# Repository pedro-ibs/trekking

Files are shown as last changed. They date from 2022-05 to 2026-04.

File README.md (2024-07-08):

# Trekking project
Desenvolvimento de um robô rádio-controlado/autônomo da moralidade “trekking”

Nos arquivos [anteriores-descontinuados](./anteriores-descontinuados/) e nos demais arquivos deste repositório podem conter os termos `rv1` e `rv2` eles estão referindo a versões anteriores do robô sendo `Robô versão 1` `Robô versão 2`.

<br>

Apresentações anteriores relaionadas:
 * [**#CPBR16** - Trabalhando com Unidades de medidas Inerciais (IMU) ](https://garoa.net.br/wiki/Dumont_Hackerspace_na_Campus_Party_2024)
 * [ **#CPBR15** - Construindo um Robô Trekking - versão 2.0](https://www.youtube.com/watch?v=lGhopql1V54)
 * [ **#CPBR14** - Construção de um robo rádio controlado](https://www.youtube.com/watch?v=8P9nPsCdVAc)

<br> <br> <br>

### **Robô versão 3**:
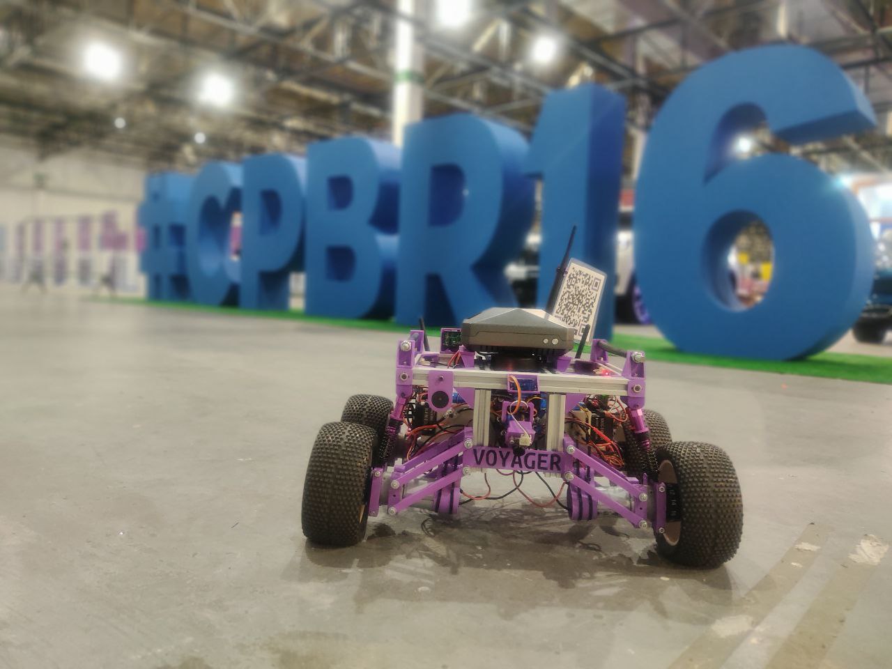
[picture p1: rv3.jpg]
Robô versão 2


<br>

### **Robô versão 2**: 

Robô versão 2

<br>

### **Robô versão 1**: 

Robô versão 1

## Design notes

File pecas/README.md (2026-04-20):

# Peças
Todas as peças do projeto foram desenvolvidas utilizado o software [FreeCad](https://www.freecadweb.org/).

 * *[Medidas](./medidas)*
 * *[Peças 3D](./stl)*
 * Cor da montagem HEX: ```#380054``` 

### *Peças externas*

Algumas peças já existentes utilizadas no projeto

  * [Porca para perfil V-slot 20x20](https://www.thingiverse.com/thing:3050607)
  * [Star Trek Pin](https://www.thingiverse.com/thing:2798431)

<hr><br><br>

# Fabricação

Todas as peças foram fabricadas utilizando uma prototipadora Creality Ender-3, e fatiados pelo programa Ultimaker Cura.

#### Especificações *gerais* de impressão:

<br>

Parâmetro               | Valor
:---------------------- | :-------------------------------------
Adesão                  | Ativado
Nozzle                  | 0.4 mm
Densidade               | 30 %
Resolução               | 0.2

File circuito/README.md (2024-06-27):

# **ESQUEMA GERAL DA ALIMENTAÇÃO E CONEXÇÕES DO ROBÔ**

<br>

### **ALIMENTAÇÃO GERAL**
A chave `SELETOR` muda se a bateria passrá pelo voltimetro-amperimetro, ou se firará em paralelo com a carga, permitindo assim monitorar o carregamento da bateria. Também com as chaves `CIRCUITO COMUTADOR` e `CIRCUITO POTÊNCIA` permite ligar ou desligar um sistema independentemente do outro. Essas opções existem para facilitar o desenvolvimento e manutenção do robô

<br>

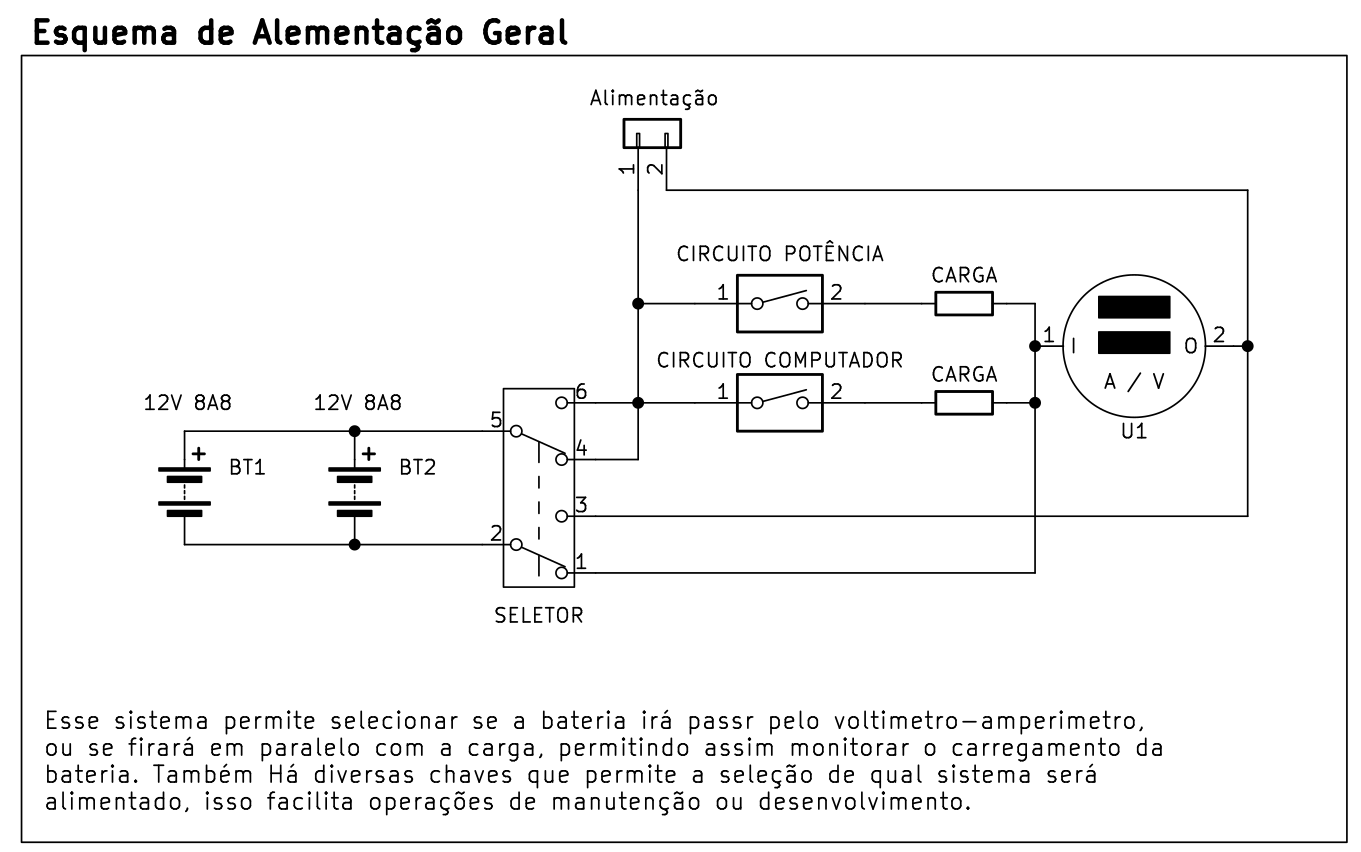
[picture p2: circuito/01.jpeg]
ALIMENTAÇÃO GERAL


<br> <br>

### **ALIMENTAÇÃO DOS SUBSISTEMAS**
Para o Robô a linha de `POTÊNCIA` é considerada a de 12V, que irá alimentar os motores e atuadores que demandam uma corrente elevada. Já a linha `COMPUTADOR` é responsável por alimentar o sistema de controle principal e alguns subsistemas.

<br>

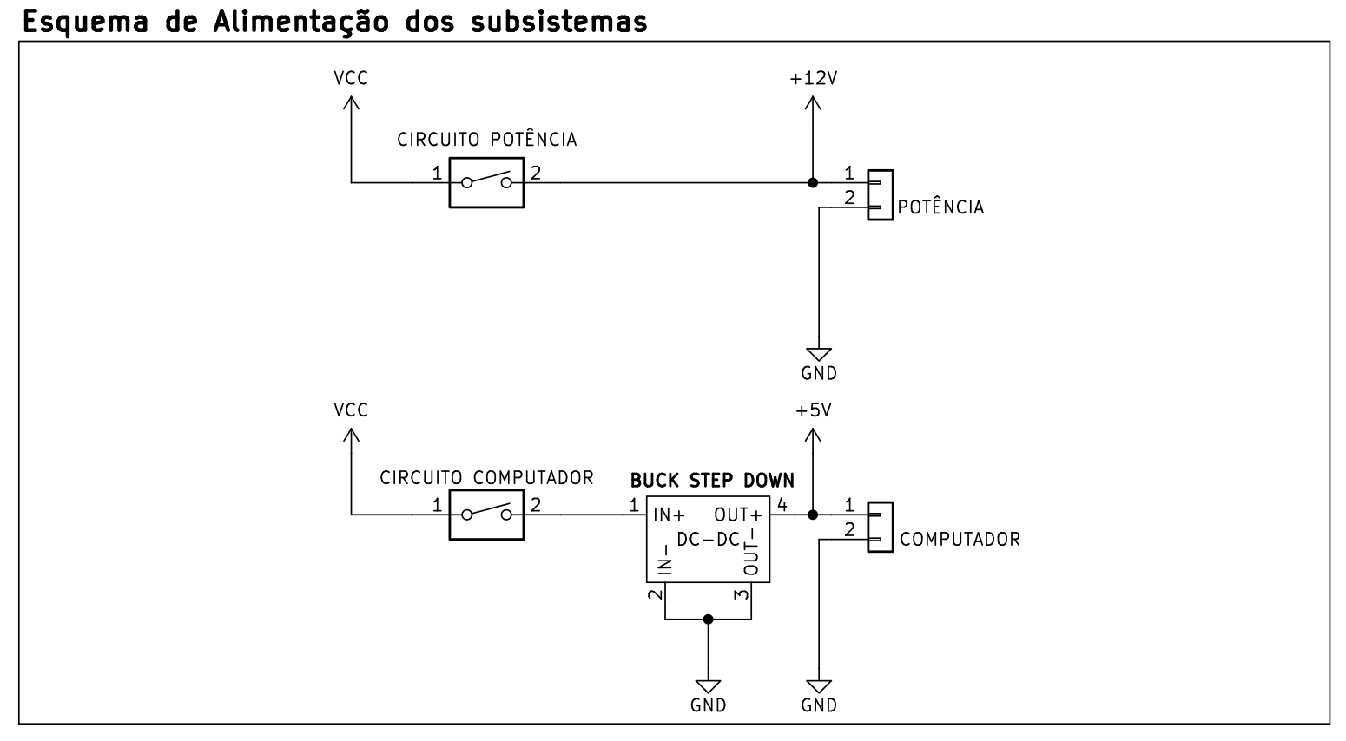
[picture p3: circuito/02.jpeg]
ALIMENTAÇÃO DOS SUBSISTEMAS


<br> <br>

### **ALIMENTAÇÃO DOS SUBSISTEMAS**
O robô contém alguns subsistemas, dois reservados para controlar os conjuntos de motores esquerdos e direitos, e um responsável pelo controle de ativação e controle ativo sensores e atuadores, também faz a aquisição de alguns sensores.

<br>

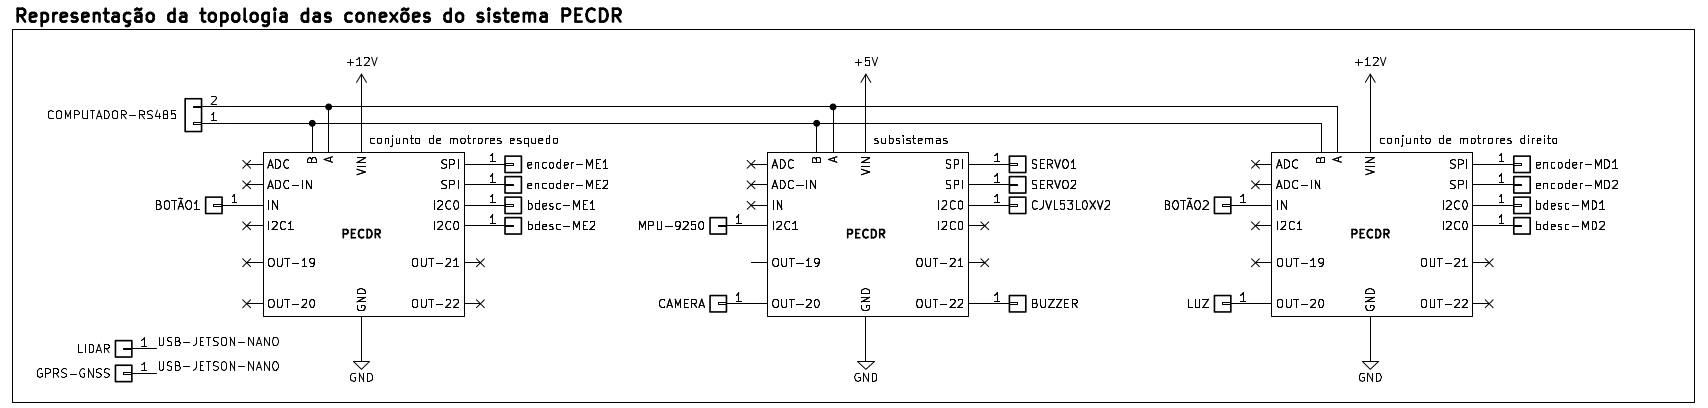
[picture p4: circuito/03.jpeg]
TOPOLOGIA E CONEXÕES DOS SUBSISTEMAS


<br>

### **Topologia das conexõesdo dos motores**

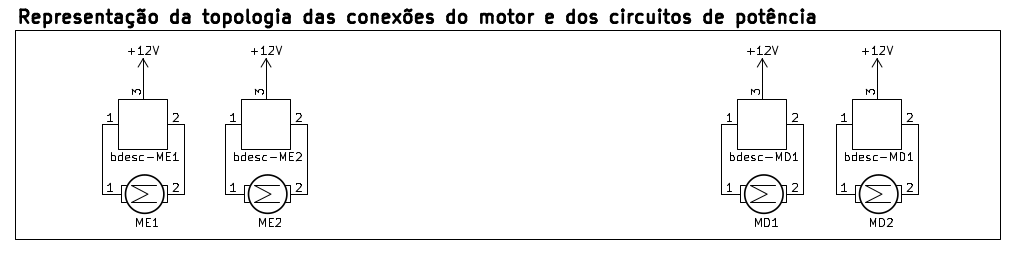
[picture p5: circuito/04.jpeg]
Topologia das conexõesdo dos motores


<br> <br>

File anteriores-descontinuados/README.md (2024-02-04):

# **Anteriores / Descontinuados**

Conforme as alterações e evolução do robô algumas ideias foram descontinuadas, então aqui contém alguns arquivos de versões passadas como circuitos, peças e configurações. Não há intenção de mexer ou documentar mais esses arquivos já que eles não fazem mais parte do robô.

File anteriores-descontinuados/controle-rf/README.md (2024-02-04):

# **controle-rf**

<br>

Testes de um controle RF construído para controlar o robô em longas distâncias. O controle utiliza o `Modulo Rf 433mhz Wireless Hc-12` e uma `microbit v1`.

<br>

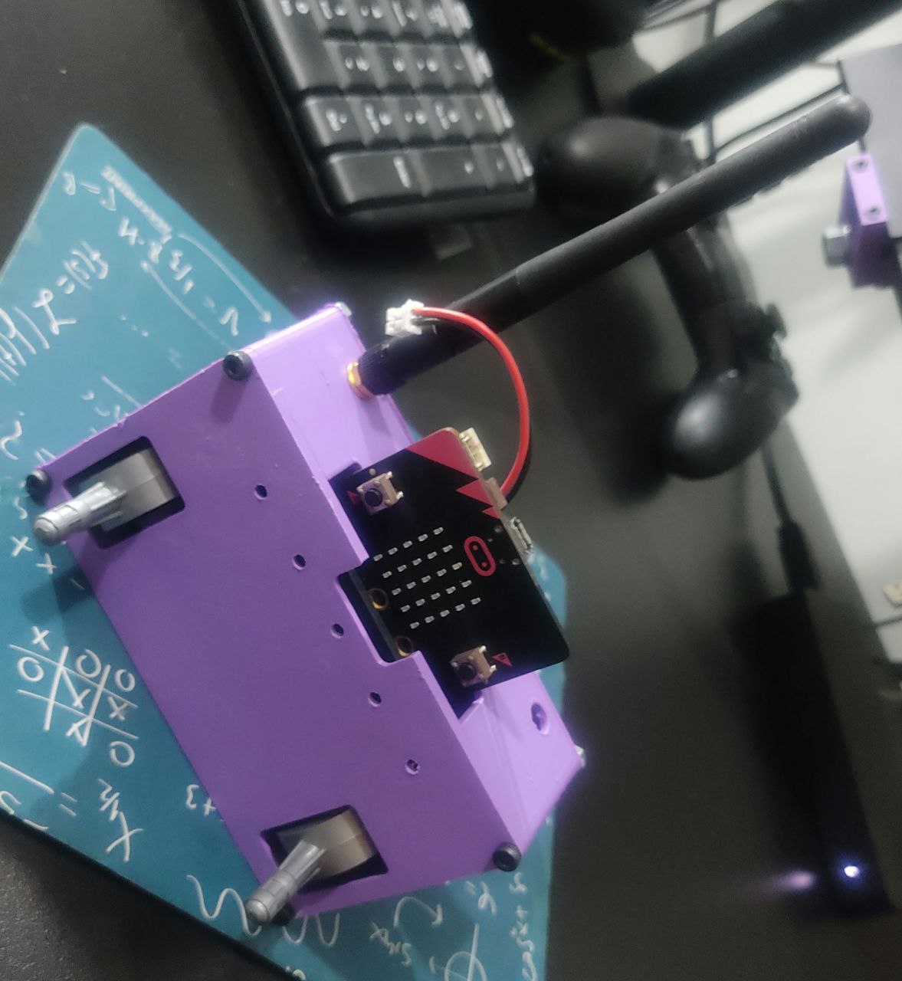
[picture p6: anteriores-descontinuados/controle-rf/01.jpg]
trekking vista da base e suporte da base


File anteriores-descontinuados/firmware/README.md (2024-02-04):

# **Firmware**

1. [**`NANO_BLE_33S`**](./NANO_BLE_33S): Auxiliar na aquisição de dados dos sensores.

2. [**`RPI_PICO_SDK`**](./RPI_PICO_SDK/): Controle dos motores e possível modulo de expansão. Tem acesso aos drivers dos motores portando responsável pelo controle dos mesmos.

## **Componentes**

O Trekking é composto por alguns dispositivo dentre sensores e computador e microcontroladores:

 * [Raspberry Pi 3 Model B](https://www.raspberrypi.com/products/raspberry-pi-3-model-b/)
 * [Raspberry Pi Pico](https://www.raspberrypi.com/products/raspberry-pi-pico/)
 * [Arduino Nano 33 BLE Sense](https://docs.arduino.cc/hardware/nano-33-ble-sense)
   * [IMU 9 Eixos LSM9DS1](https://content.arduino.cc/assets/Nano_BLE_Sense_lsm9ds1.pdf)
   * [Barometro LPS22HB](https://content.arduino.cc/assets/Nano_BLE_Sense_lps22hb.pdf)
   * [Sensor de Temperaura e Umidade HTS221](https://content.arduino.cc/assets/Nano_BLE_Sense_HTS221.pdf)
   * [Sensor de Gestos APDS-9960](https://content.arduino.cc/assets/Nano_BLE_Sense_av02-4191en_ds_apds-9960.pdf)
   * [Microfone MP34DT05](https://content.arduino.cc/assets/Nano_BLE_Sense_mp34dt05-a.pdf)
 * [GPRS GT-U7](https://manuals.plus/goouuu/goouuu-tech-gt-u7-gps-modules.pdf)
 * [Sensor de distância CJVL53L0XV2 / VL53L0X](https://www.st.com/resource/en/datasheet/vl53l0x.pdf)

 Esses dispositivo estão interconectados através das comunicações serias *usart*, *i2c* e *swd* como mostra o diagrama abaixo:

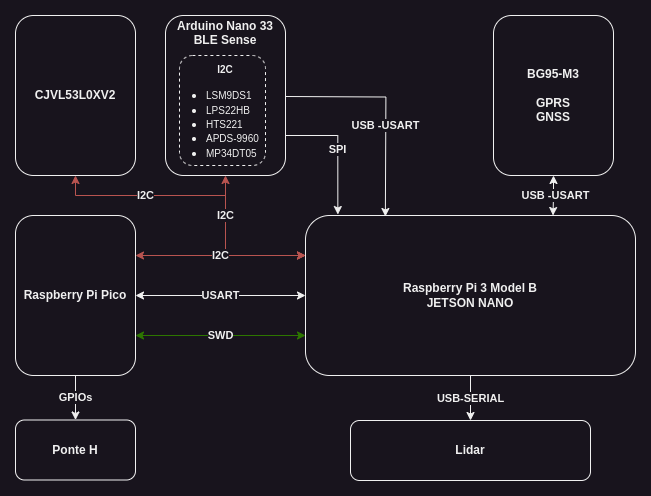
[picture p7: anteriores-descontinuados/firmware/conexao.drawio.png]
Rede de conexão entre os sensores e dispositivos do trekking


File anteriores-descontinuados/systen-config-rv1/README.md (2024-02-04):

# **NOTA:** 

<br>

Pode haver incoerências no processo e ou incompatibilidade nos funcionamentos pois esses arquivos retratam uma versão antiga e descontinuada do robô, eles estão aqui por uma questão de histórico.

<br><br><br>

# **systen-config-rv1**

<br>

1. Instale es dependências:

```
sudo apt update -y
sudo apt upgrade -y
sudo apt install python3-pip evdev -y

pip3 install evdev 
pip3 install pyserial 
```

2. copie o arquivo `gameped.py` para o diretório:

```
mkdir -p ~/trekking
cp gameped.py ~/trekking/gameped.py
```

3. Terne o arquivo executável:

```
sudo chmod +x ~/trekking/gameped.py
```

4. edite o arquivo `/etc/rc.local` antes da linha com o comando `exit` e insira o seguinte comando:
```
sudo python3  ~/trekking/gameped.py &
```

5. Reinicie a raspberry e logo após um tempo insira o adaptador do controle ela irá reconhecer automaticamente 

### **NOTA:**
Foi utilizado o controle `Ipega 9076` para esse programa.

6. Intale o node-red seguindo esses [paços](https://nodered.org/docs/getting-started/raspberrypi).

7. Importe o [flows-RASPBERRY_PI.json](./flows-RASPBERRY_PI.json) para o node-red.

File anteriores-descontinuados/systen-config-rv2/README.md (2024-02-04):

# **NOTA:** 

<br>

Pode haver incoerências no processo e ou incompatibilidade nos funcionamentos pois esses arquivos retratam uma versão antiga e descontinuada do robô, eles estão aqui por uma questão de histórico. 

<br><br><br>

# **systen-config-rv2**

<br>

1. Instale es dependências:

```
sudo apt update -y
sudo apt upgrade -y
sudo apt install python3-pip evdev -y

pip3 install evdev 
pip3 install pyserial 
```

2. Com o arquivo `gameped-rv2.py` e `gamepad-rv2-server.service` crie um no sistema por meio do systemctl.

3. Intale o node-red seguindo esses [paços](https://nodered.org/docs/getting-started/raspberrypi).

4. Importe o [flows-JETSON_NANO.json](./flows-JETSON_NANO.json) para o node-red.

### **NOTA:**
Foi utilizado o controle `Ipega 9076` para esse programa.

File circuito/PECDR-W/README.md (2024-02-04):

# **PECDR** - **P**lataforma **E**letrónica de **C**ontrole **D**istribuído em **R**ede 

A proposta deste circuito é distribuir o controle em subsistemas utilizando rede sem fio ou por meio da comunicação RS485. Conta com a `raspberry pi pico` modelo comum ou `W`. e diversos periféricos possibilitando atuar em trabalhos variados.

### **Elementos**:
 * O circuito embarca uma `raspberry pi pico` modelo comum ou `W`;
 * Uma fonte dc-dc buck step down 3V3 3A;
 * Driver de potência  L298N (com seleção de tensão de operação entre VCC e 3V3);
 * Interface de comunicação RS485;
 * Disponibiliza GPIOS para uso geral; 
 * Expansão para o MPU9250/6500;

<br>

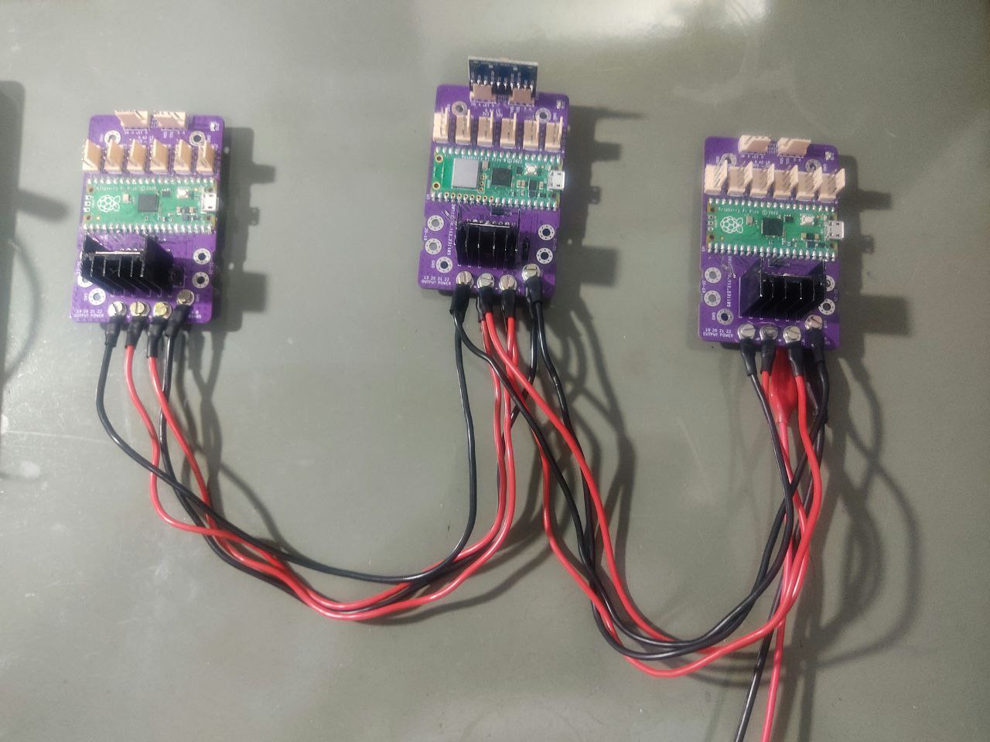
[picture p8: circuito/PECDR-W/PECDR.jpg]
imagem do circuito em rede RS485


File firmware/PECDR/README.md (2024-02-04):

# **PECDR** - **P**lataforma **E**letrónica de **C**ontrole **D**istribuído em **R**ede 

<br>

Veja a documentação do circuito [aqui](../../circuito/PECDR-W/README.md).

<br>

O robô está dividido em diversos subsistemas, como conjunto de motores esquerdo,  conjunto de motores direito e outros subsistemas. Onde o sistema de controle principal controla os subsistemas por meio de uma Rede em barramento com RS485.

<br> <br>

## **NOTA**:
Essas firmwares ainda estão em desenvolvimento e os arquivos aqui presente são para o início da organização deles.

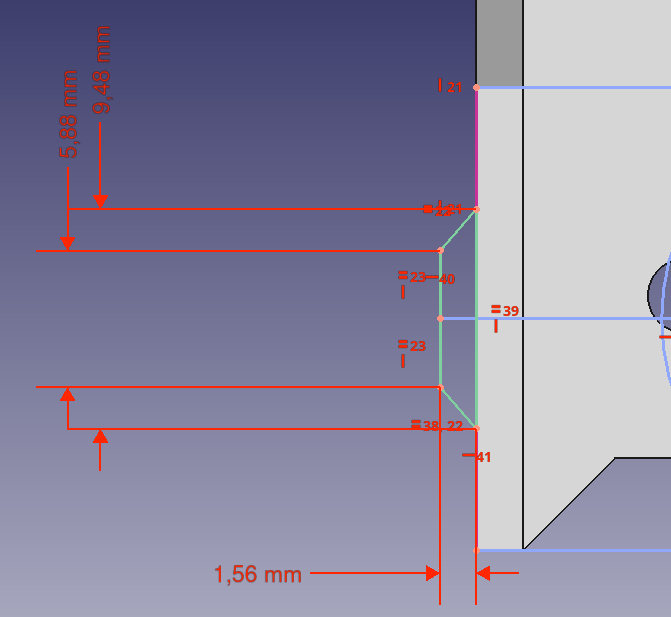
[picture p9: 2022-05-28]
pecas/medidas-trilho-rev2.png

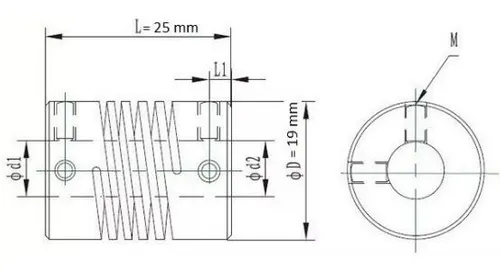
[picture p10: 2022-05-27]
anteriores-descontinuados/pecas/motor-rv1/medidas-acoplamento.webp

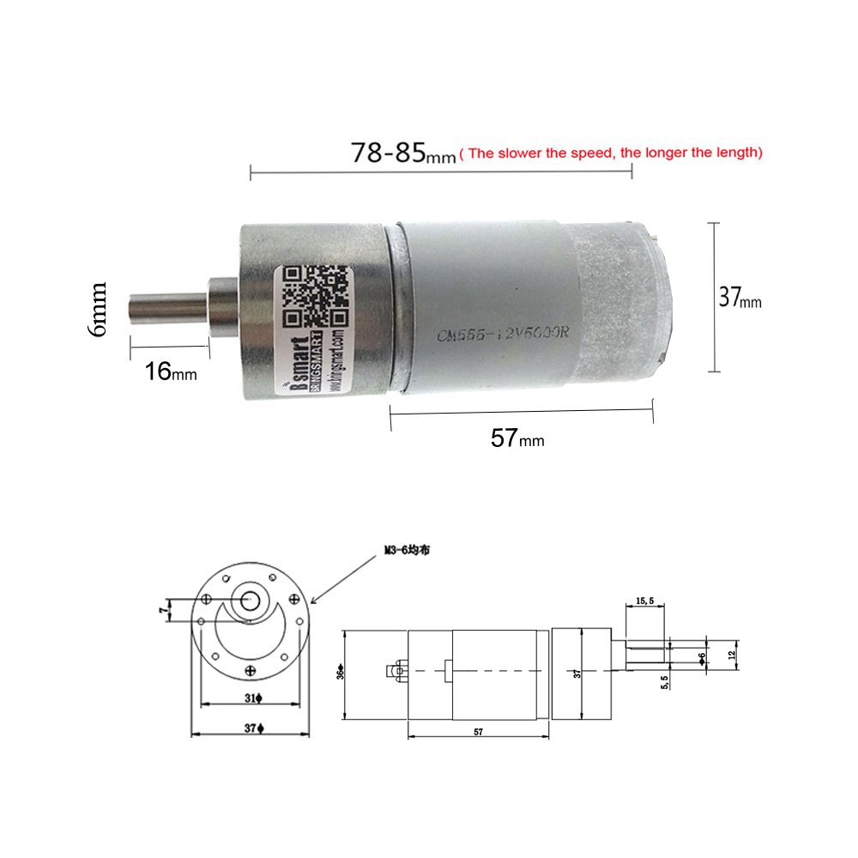
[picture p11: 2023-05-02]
anteriores-descontinuados/pecas/motor-rv2/motor2.jpg

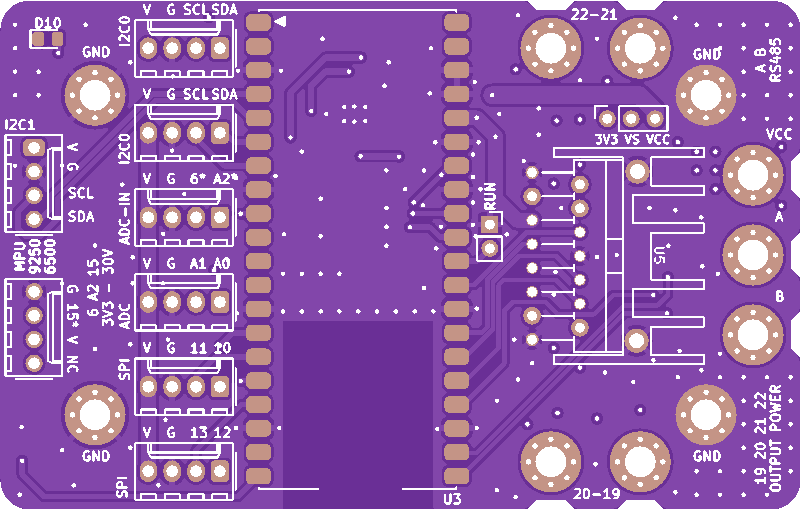
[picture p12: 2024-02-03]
circuito/PECDR-W/unnamed.png

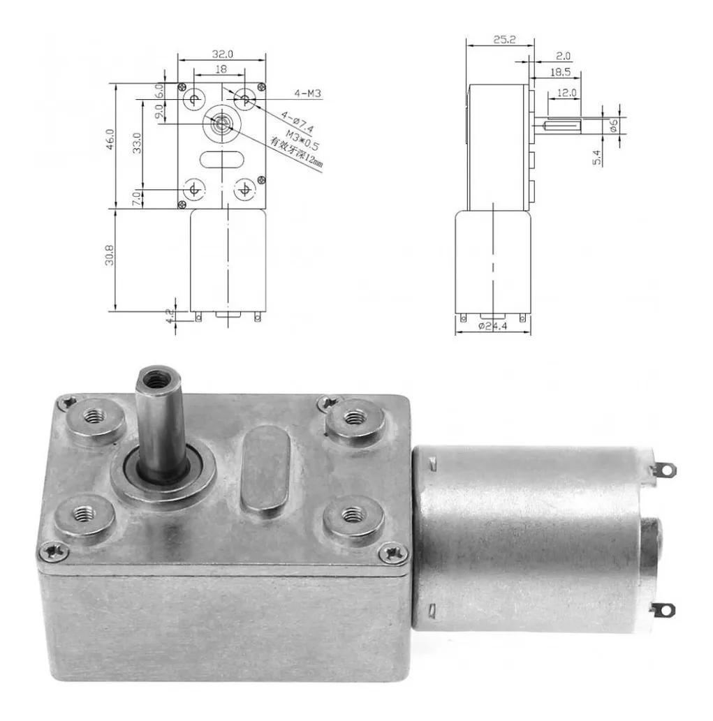
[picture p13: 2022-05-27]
anteriores-descontinuados/pecas/motor-rv1/madidas-motor.webp

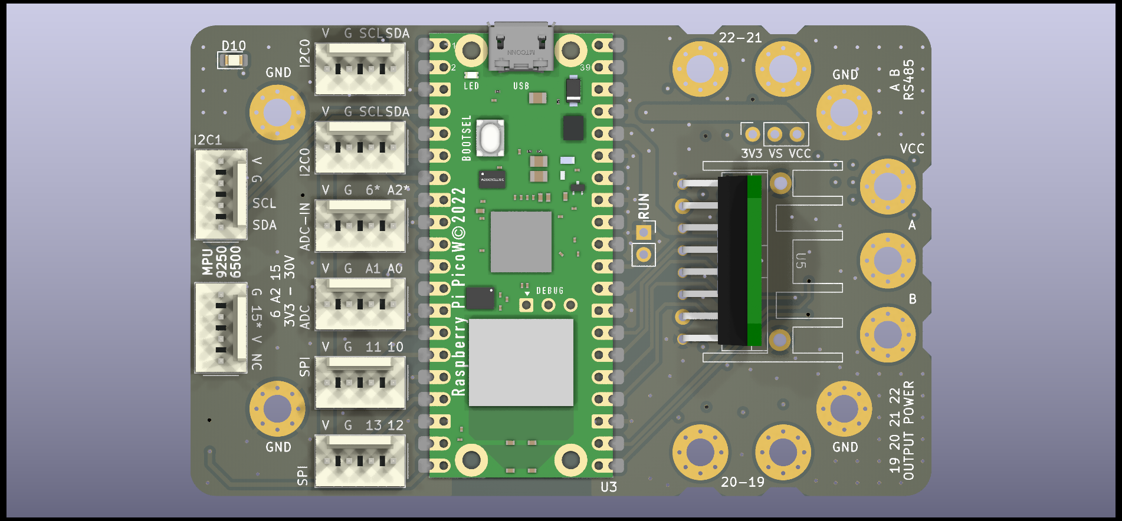
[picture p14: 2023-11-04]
circuito/PECDR-W/F-PECDR.png

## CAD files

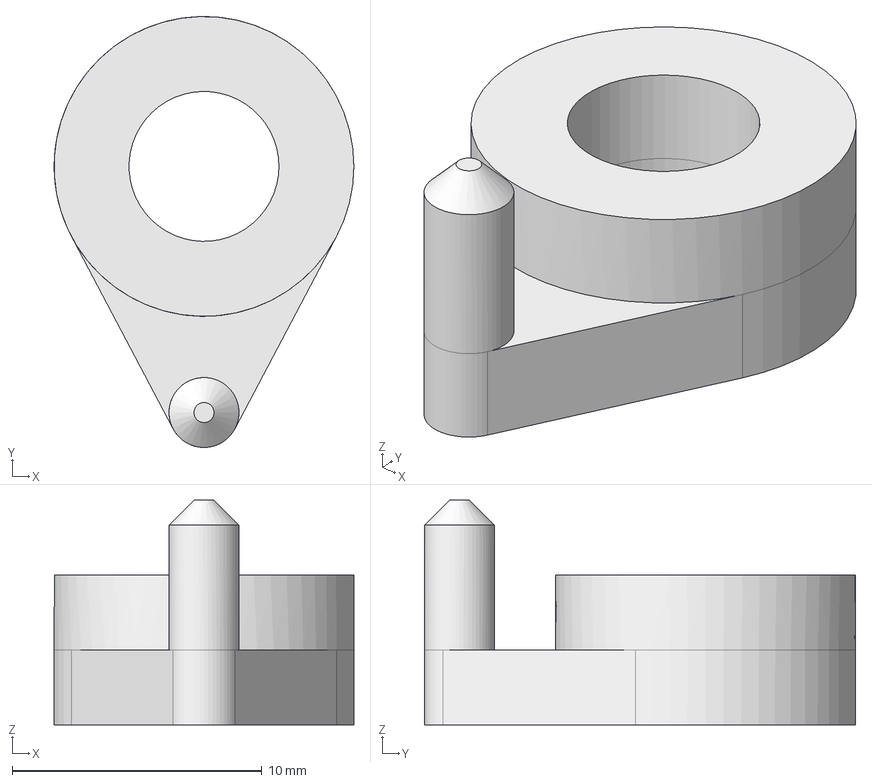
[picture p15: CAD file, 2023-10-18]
anteriores-descontinuados/controle-rf/peças/knob-pot.FCStd
12.0 x 17.2 x 9.00 mm

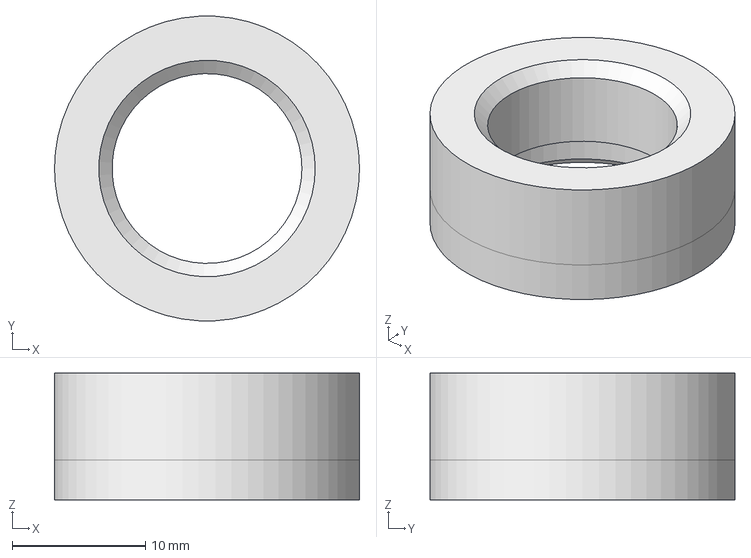
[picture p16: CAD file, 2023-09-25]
anteriores-descontinuados/pecas/camera-fpv-rv2/fisheye-coupling.FCStd
22.9 x 22.9 x 9.50 mm

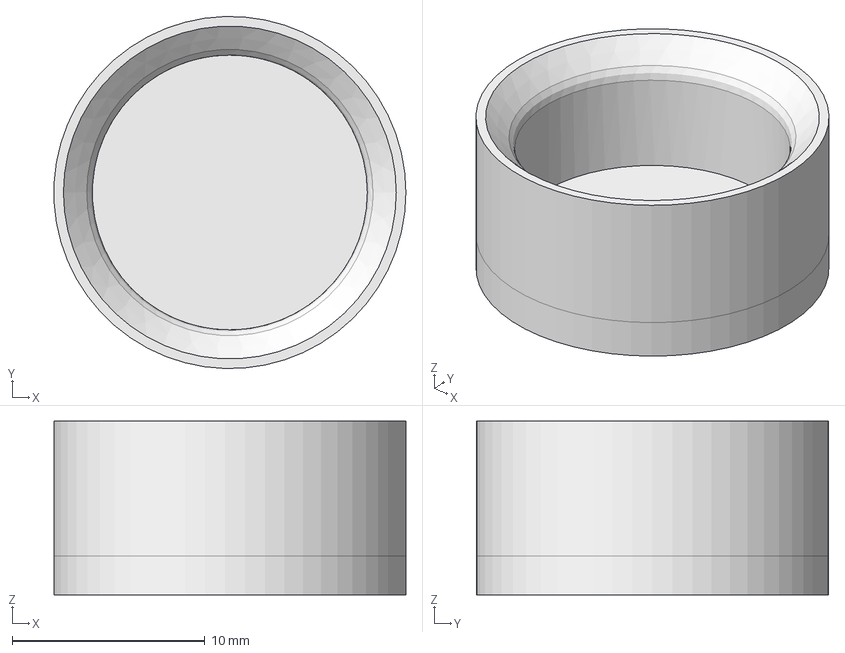
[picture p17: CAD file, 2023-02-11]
anteriores-descontinuados/pecas/camera-pi-infrared/fixed/cap.FCStd
18.2 x 18.2 x 9.00 mm

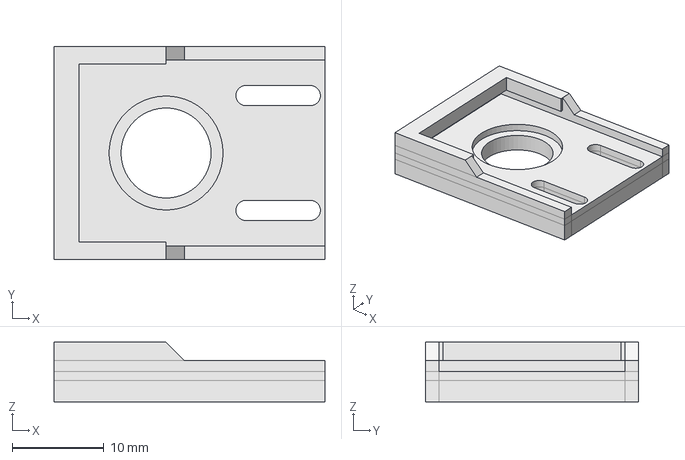
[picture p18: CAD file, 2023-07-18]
anteriores-descontinuados/pecas/camera-pi-infrared/magnetic-plug/case-lamp-base.FCStd
29.5 x 23.2 x 6.50 mm

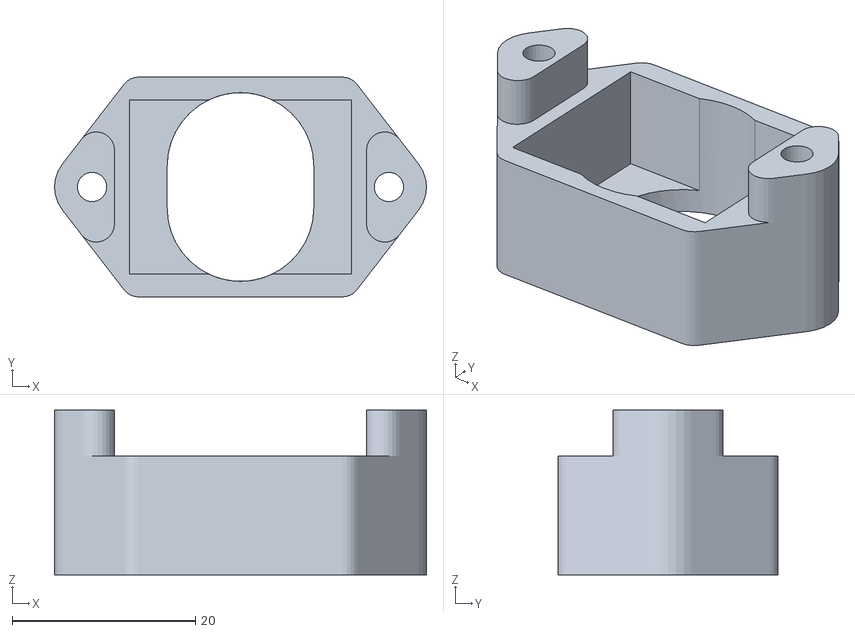
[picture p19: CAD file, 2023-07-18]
anteriores-descontinuados/pecas/camera-pi-infrared/stl/case-cam-shiled.stl
40.6 x 24.0 x 18.0

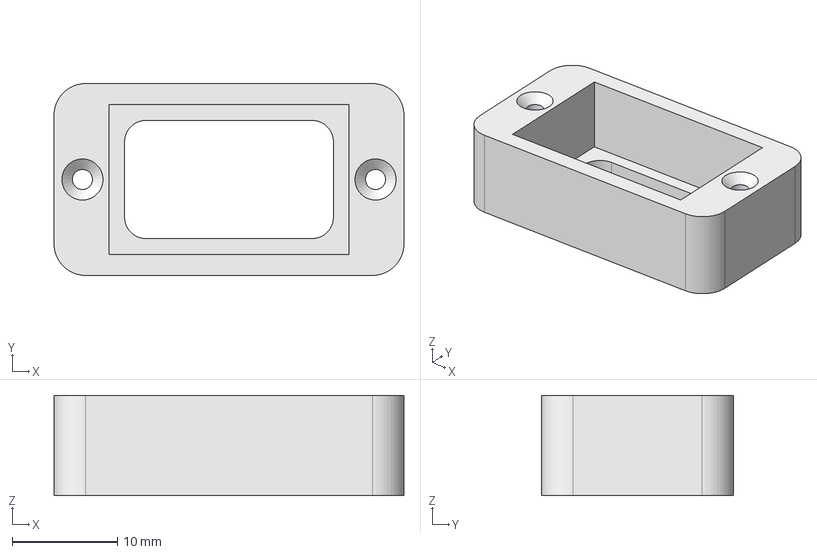
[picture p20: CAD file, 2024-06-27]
anteriores-descontinuados/pecas/case-multimetro-rv3/tampa.FCStd
33.2 x 18.2 x 9.50 mm

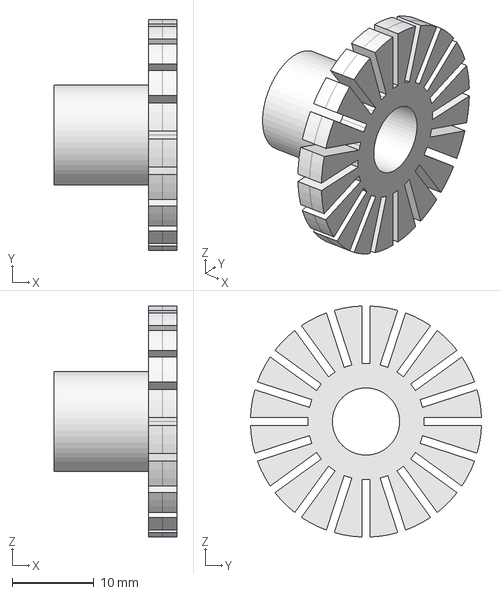
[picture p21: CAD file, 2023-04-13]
anteriores-descontinuados/pecas/encoder-rv1/disco-8d2-20P.FCStd
15.0 x 28.2 x 28.2 mm

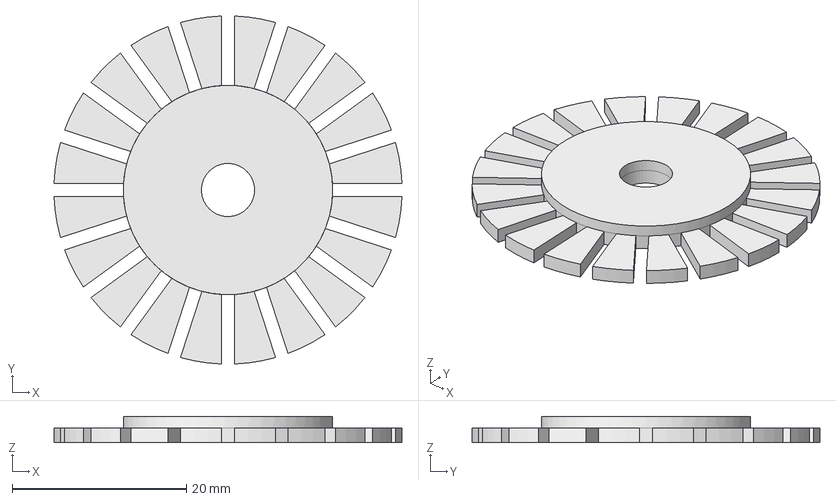
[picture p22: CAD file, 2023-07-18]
anteriores-descontinuados/pecas/encoder-vr2/disco-3d40-20P.FCStd
40.0 x 40.0 x 3.00 mm

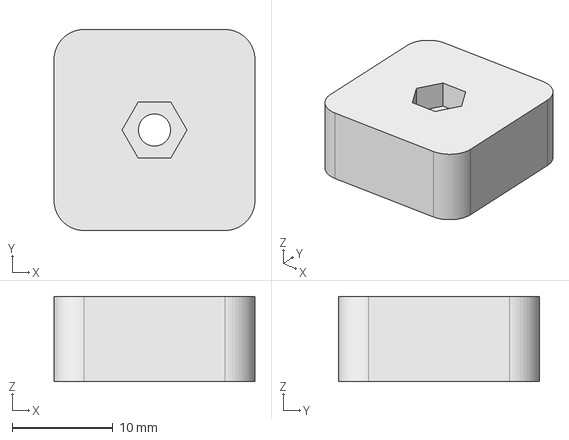
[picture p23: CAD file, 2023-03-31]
anteriores-descontinuados/pecas/lds-rv2/fixador.FCStd
20.0 x 20.0 x 8.50 mm

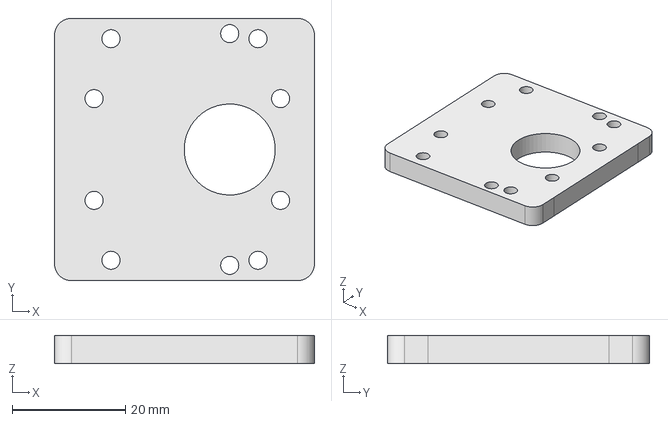
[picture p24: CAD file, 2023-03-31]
anteriores-descontinuados/pecas/motor-rv1/mancal-tras.FCStd
46.0 x 46.4 x 5.00 mm

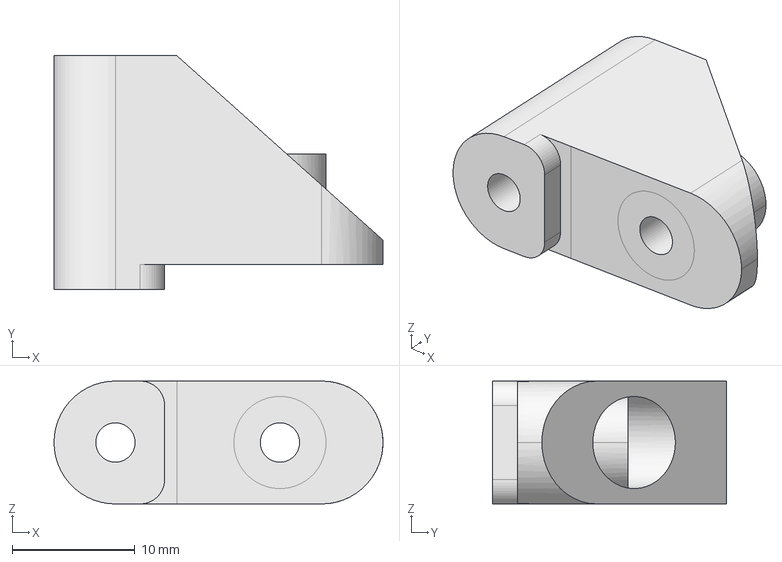
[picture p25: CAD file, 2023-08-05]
anteriores-descontinuados/pecas/motor-rv2/haste-articulada.FCStd
26.8 x 19.0 x 10.0 mm

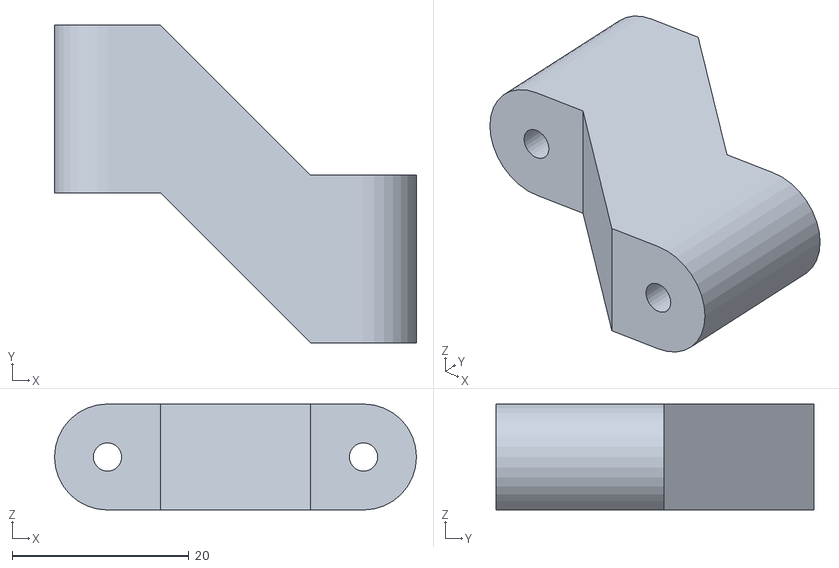
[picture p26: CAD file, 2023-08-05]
anteriores-descontinuados/pecas/motor-rv2/stl/haste.stl
41.0 x 36.0 x 12.0

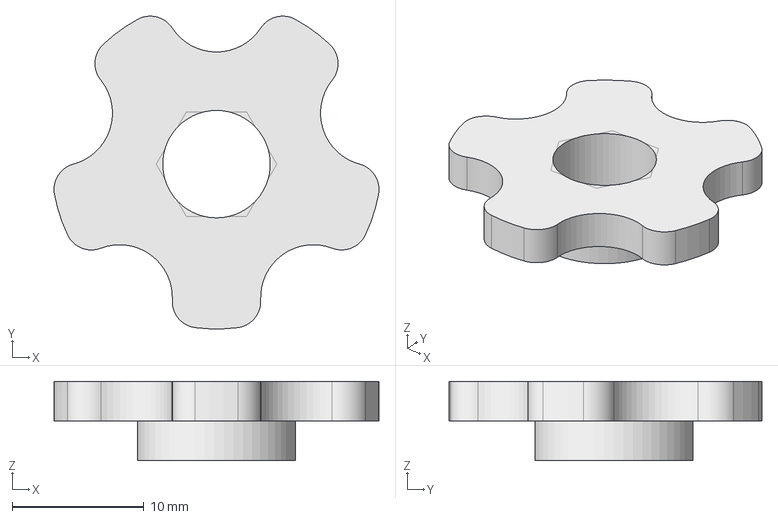
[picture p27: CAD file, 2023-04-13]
anteriores-descontinuados/pecas/roda-rv1/cap-M8.FCStd
24.6 x 23.7 x 6.00 mm

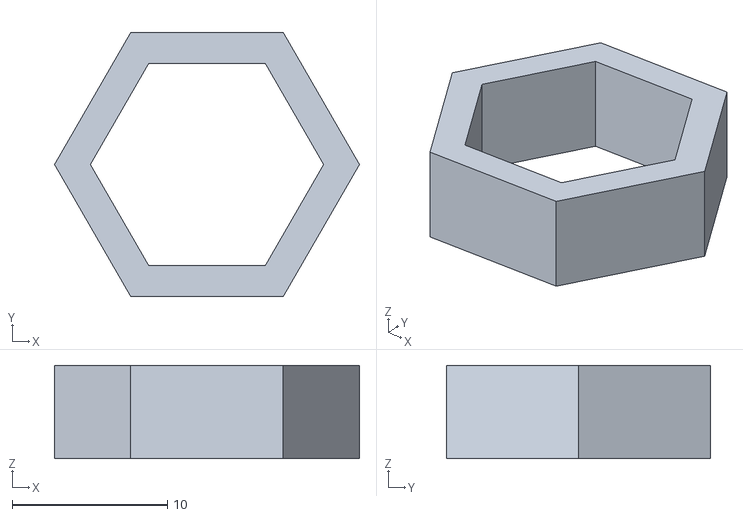
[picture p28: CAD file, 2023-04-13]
anteriores-descontinuados/pecas/roda-rv1/stl/porca-Body.stl
19.6 x 17.0 x 6.00

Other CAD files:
anteriores-descontinuados/controle-rf/peças/stl/knob-pot-Body.stl
anteriores-descontinuados/pecas/encoder-rv1/stl/disco-8d2-20P-Body.stl
anteriores-descontinuados/pecas/roda-rv2/cap-roda.FCStd
anteriores-descontinuados/pecas/roda-rv2/stl/bocal-fixadora2-Body.stl
anteriores-descontinuados/controle-rf/peças/battery-tampa.FCStd
anteriores-descontinuados/controle-rf/peças/bottom-side-case.FCStd
anteriores-descontinuados/controle-rf/peças/stl/battery-tampa-Body.stl
anteriores-descontinuados/controle-rf/peças/stl/bottom-side-case-Body.stl
anteriores-descontinuados/controle-rf/peças/stl/top-side-case-Body.stl
anteriores-descontinuados/controle-rf/peças/top-side-case.FCStd
anteriores-descontinuados/pecas/camera-fpv-rv2/shield.FCStd
anteriores-descontinuados/pecas/camera-fpv-rv2/stl/fisheye-coupling.stl
anteriores-descontinuados/pecas/camera-fpv-rv2/stl/shield.stl
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

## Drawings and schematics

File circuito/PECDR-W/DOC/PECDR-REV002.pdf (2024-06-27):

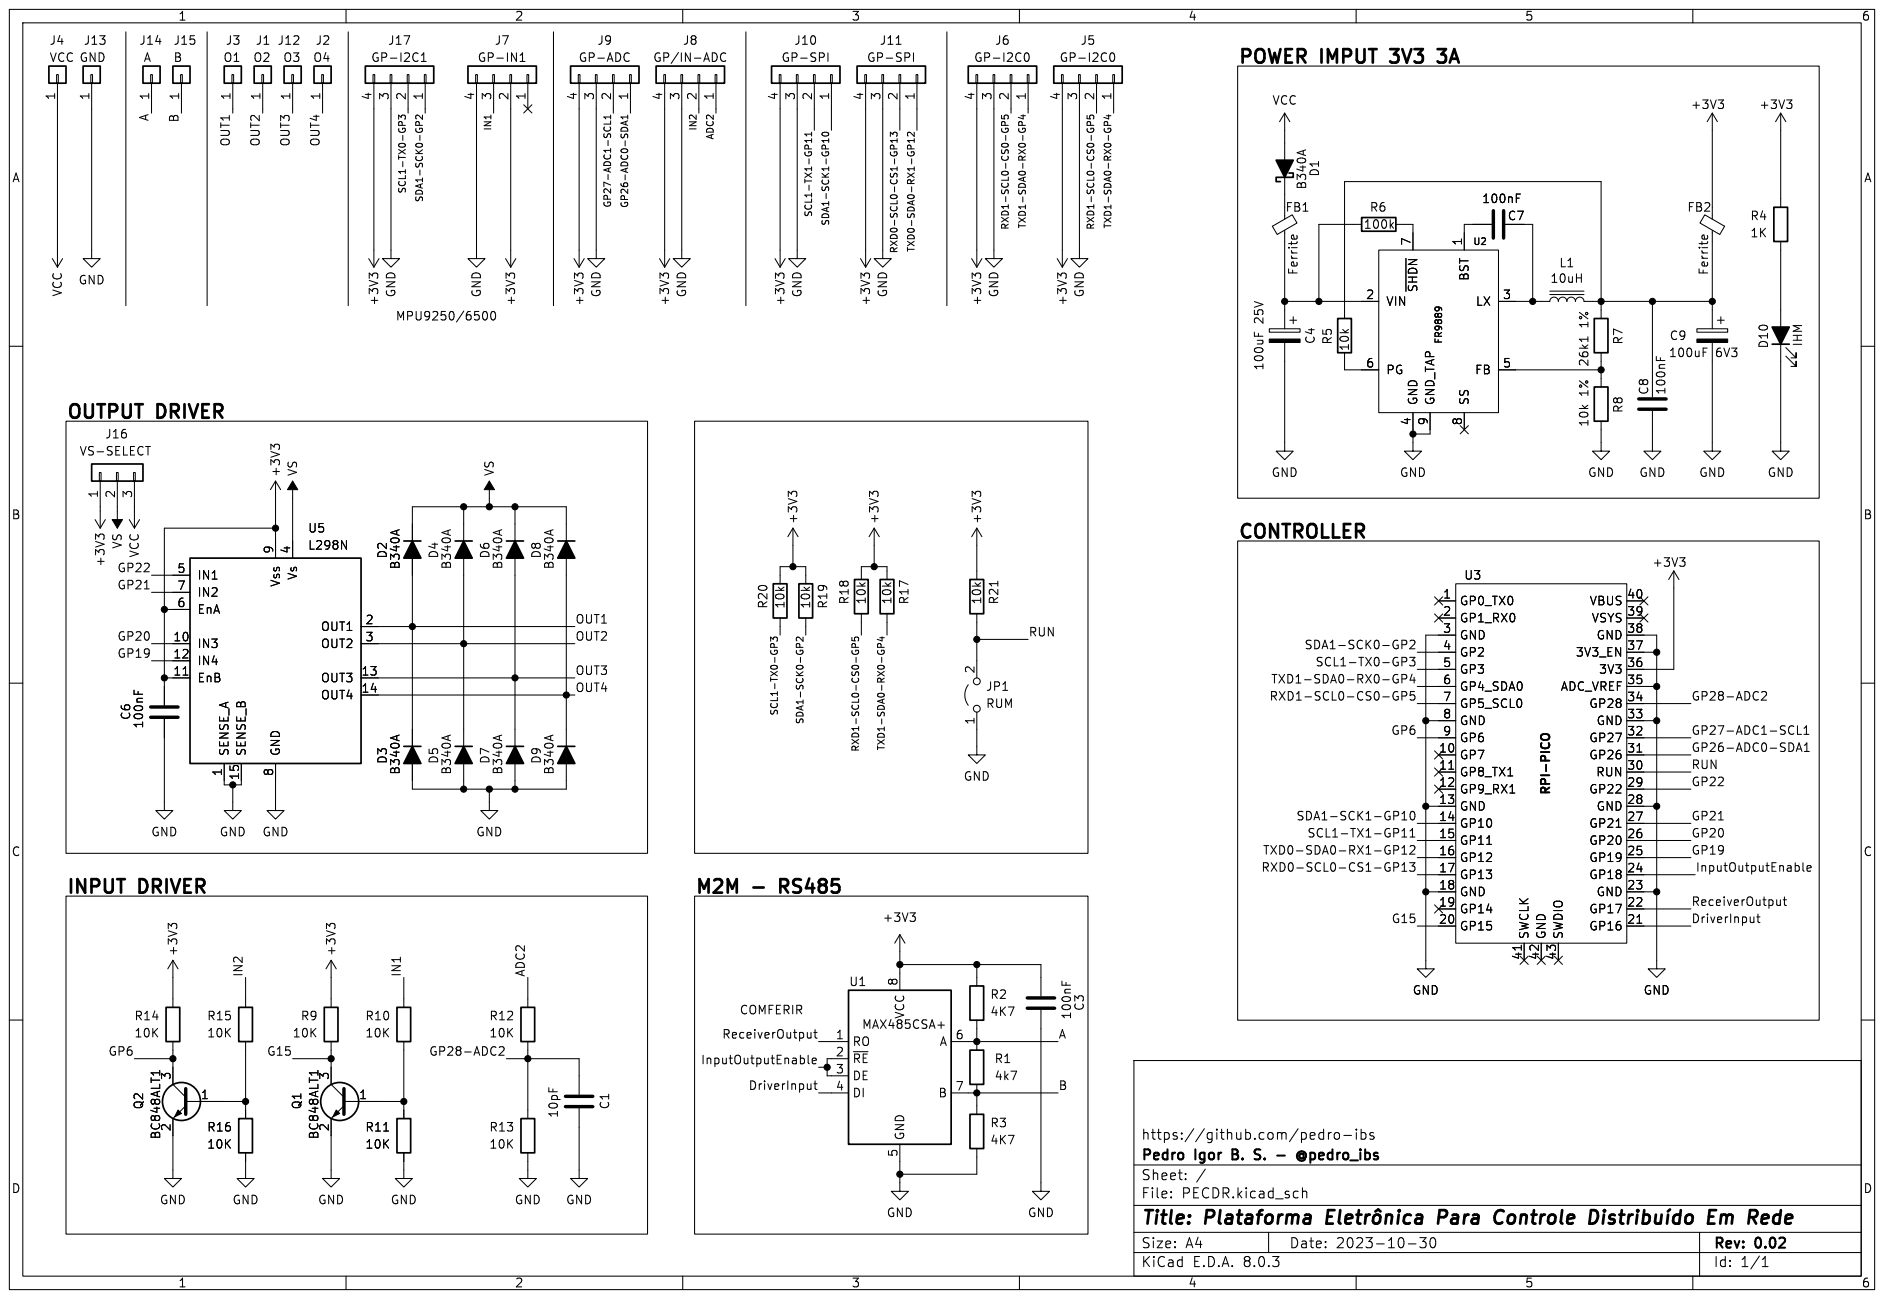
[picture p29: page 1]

2 3 Q2 BC848ALT1 GND GND GND C1 10pF GND D1 B340A BST

4 FB 5 PG 6 ~{SHDN}7 SS

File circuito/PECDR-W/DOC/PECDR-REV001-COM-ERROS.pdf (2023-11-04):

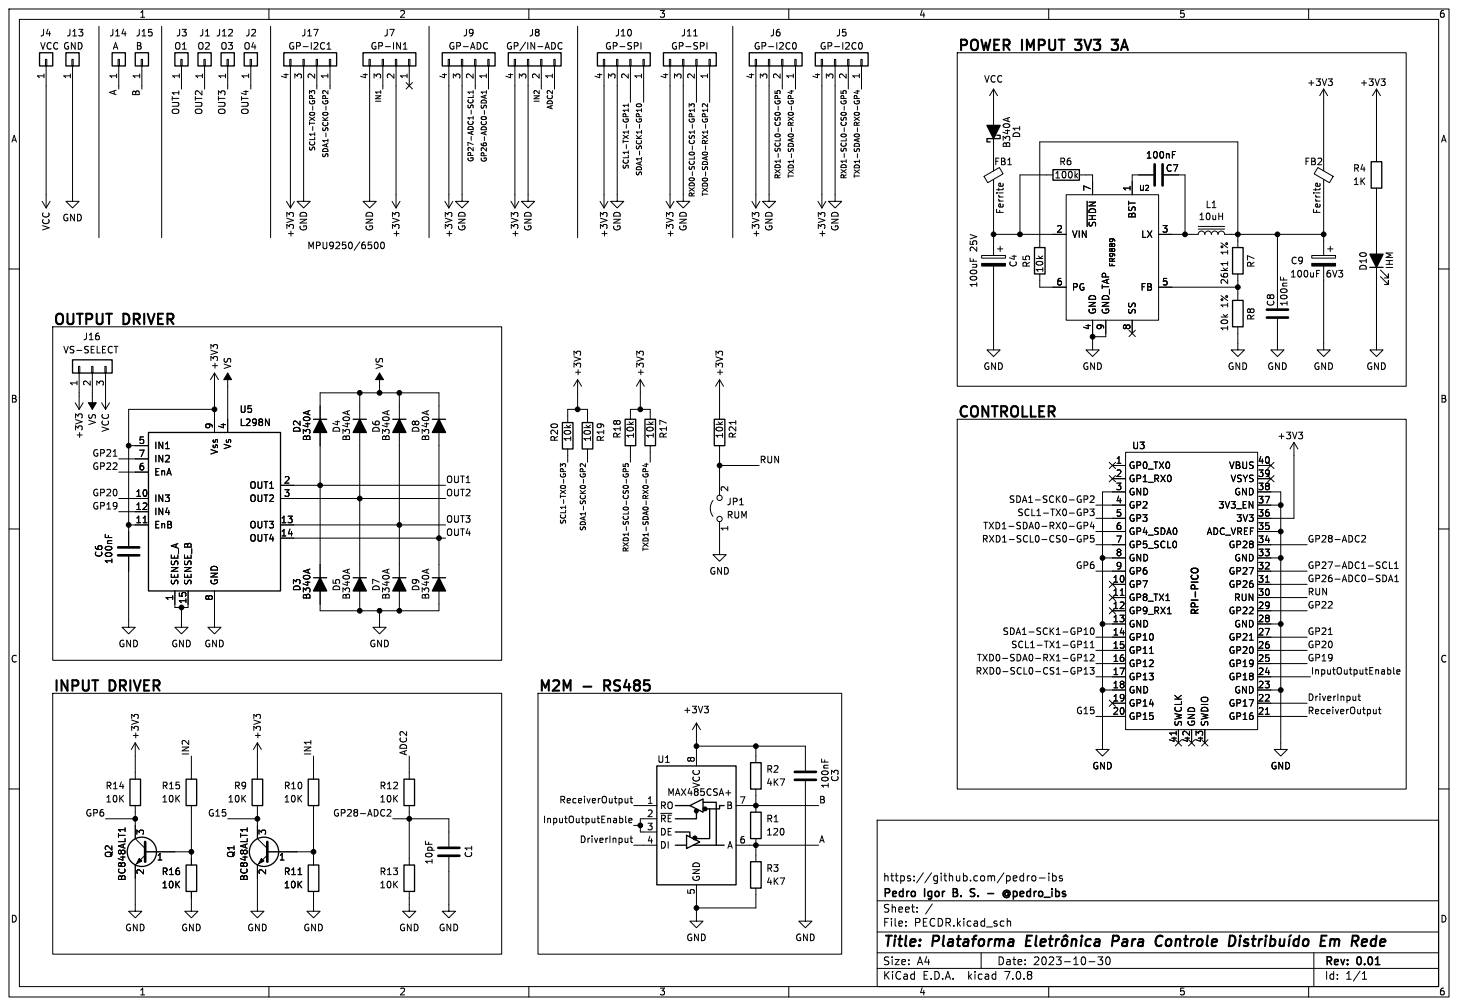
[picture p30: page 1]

J10 GP-SPI GND +3V3 GND

4 FB 5 PG 6 ~{SHDN}7 SS

https://github.com/pedro-ibs

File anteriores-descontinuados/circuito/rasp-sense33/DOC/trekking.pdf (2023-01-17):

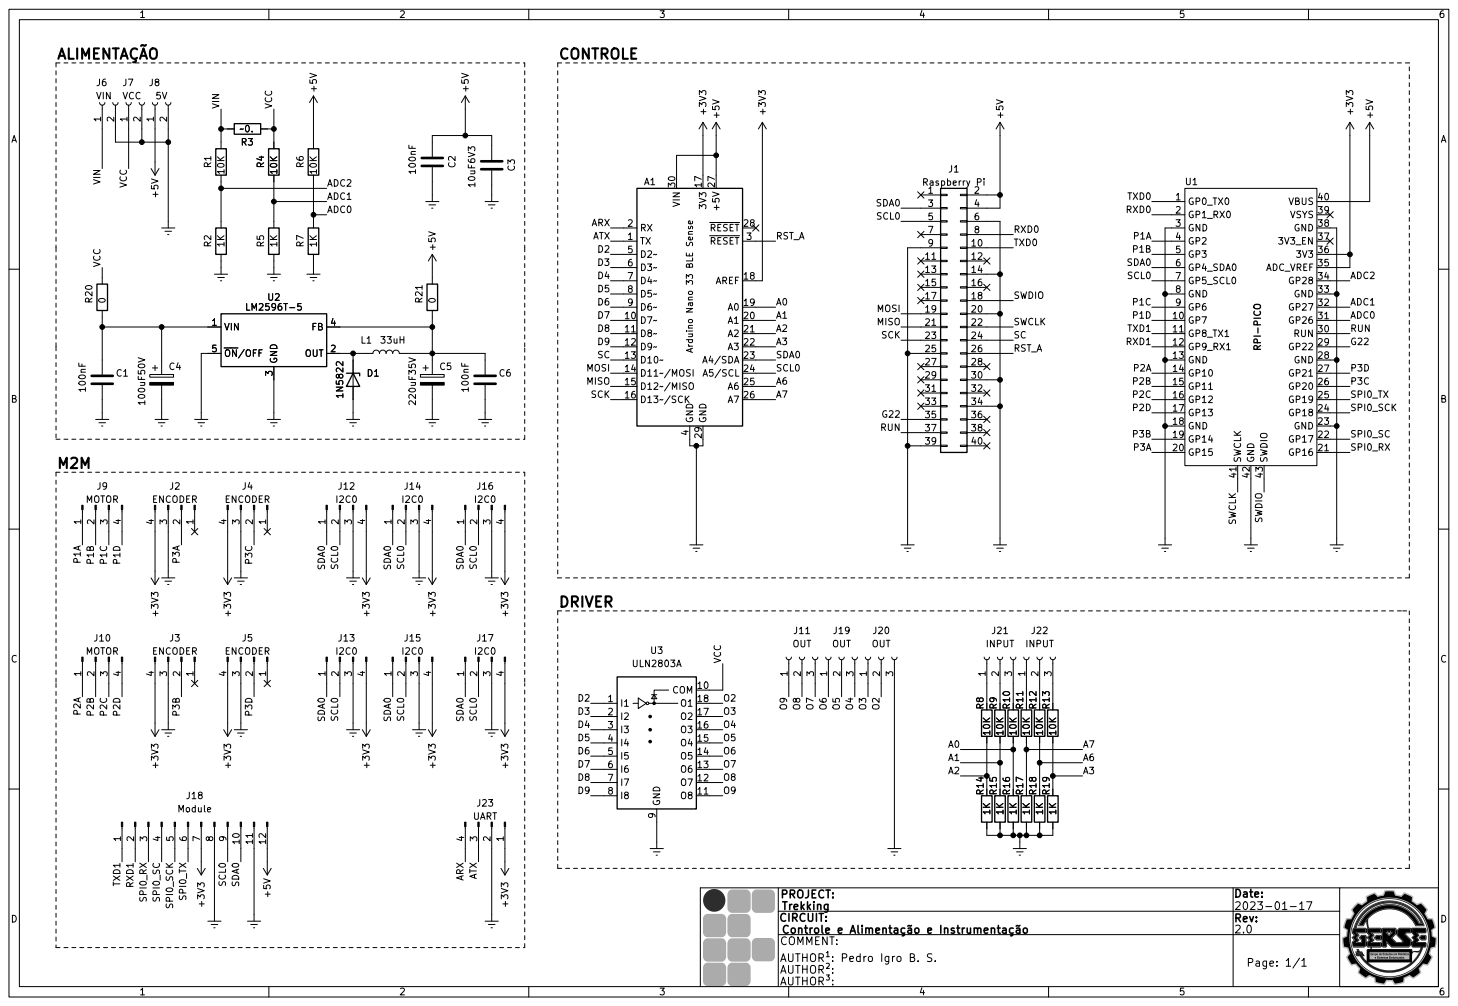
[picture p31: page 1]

4 D2~ 5 D3~ 6 D4~ 7 D5~ 8 D6~ 9 A1 Arduino Nano 33 BLE Sense C3 10uF6V3 R2 1K C4 100uF50V
J1 Raspberry Pi +5V

þÿAUTHOR²: COMMENT: þÿAUTHOR³: PROJECT: CIRCUIT:
Trekking

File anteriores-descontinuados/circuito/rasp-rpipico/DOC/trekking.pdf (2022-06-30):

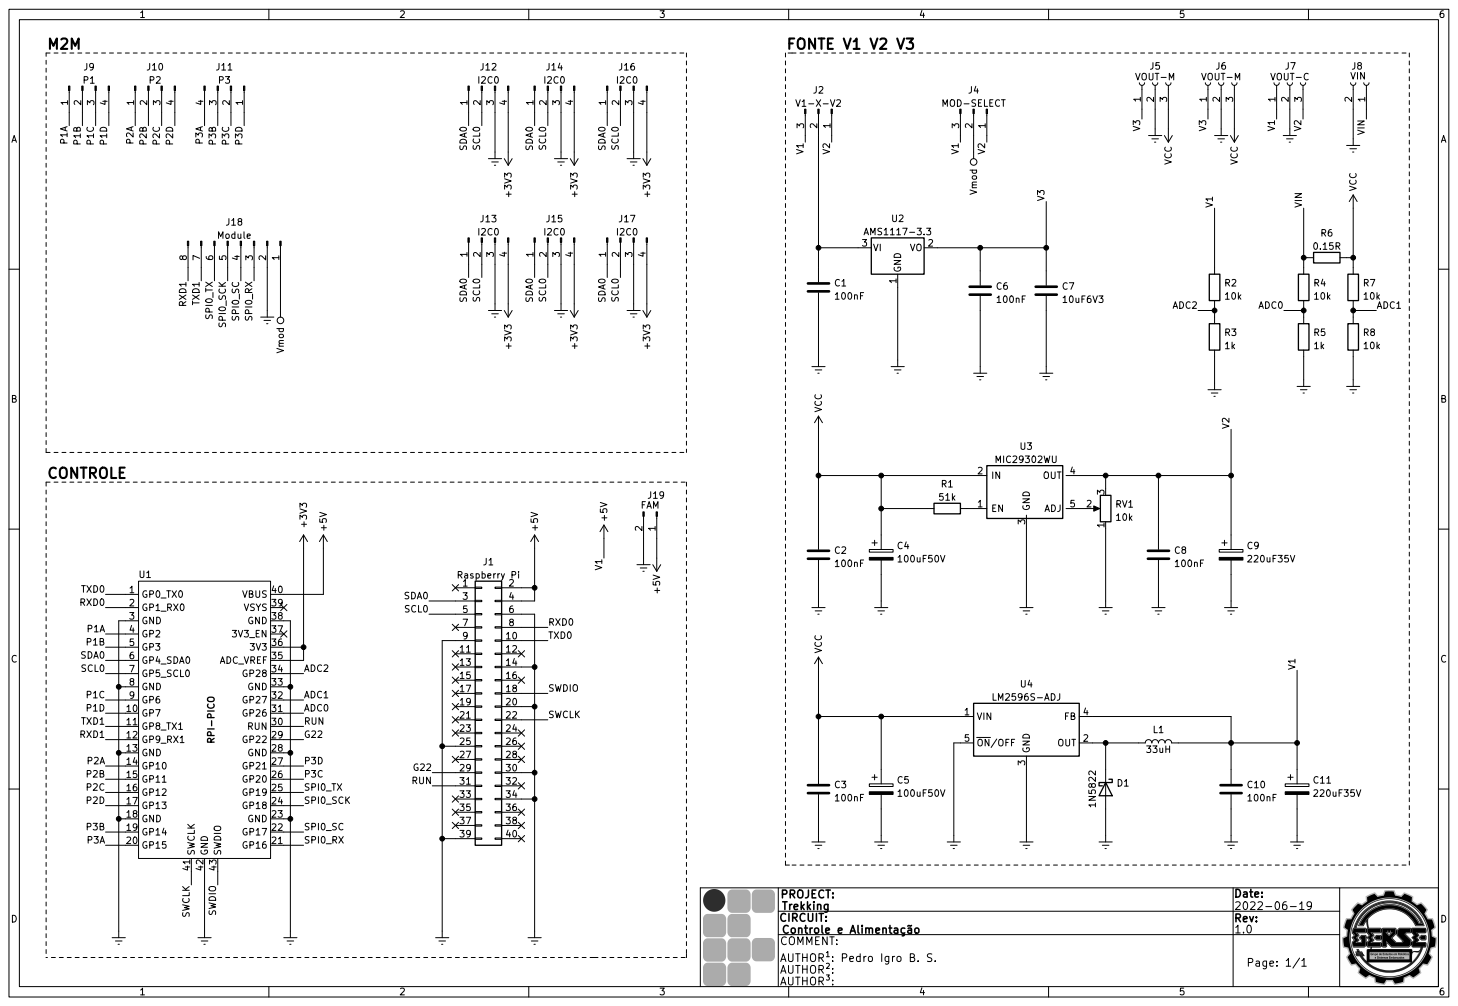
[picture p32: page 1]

þÿAUTHOR²: COMMENT: þÿAUTHOR³: PROJECT: CIRCUIT:
Trekking

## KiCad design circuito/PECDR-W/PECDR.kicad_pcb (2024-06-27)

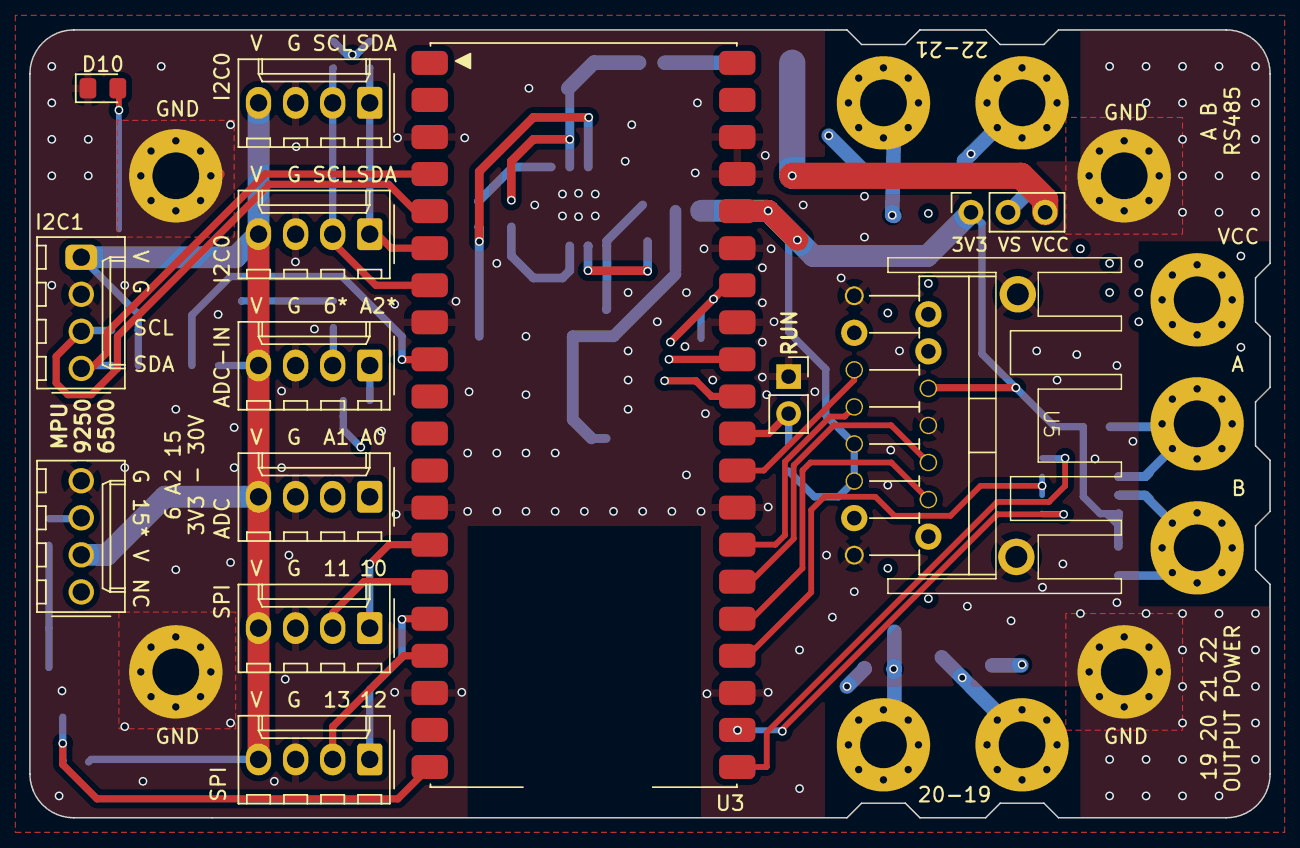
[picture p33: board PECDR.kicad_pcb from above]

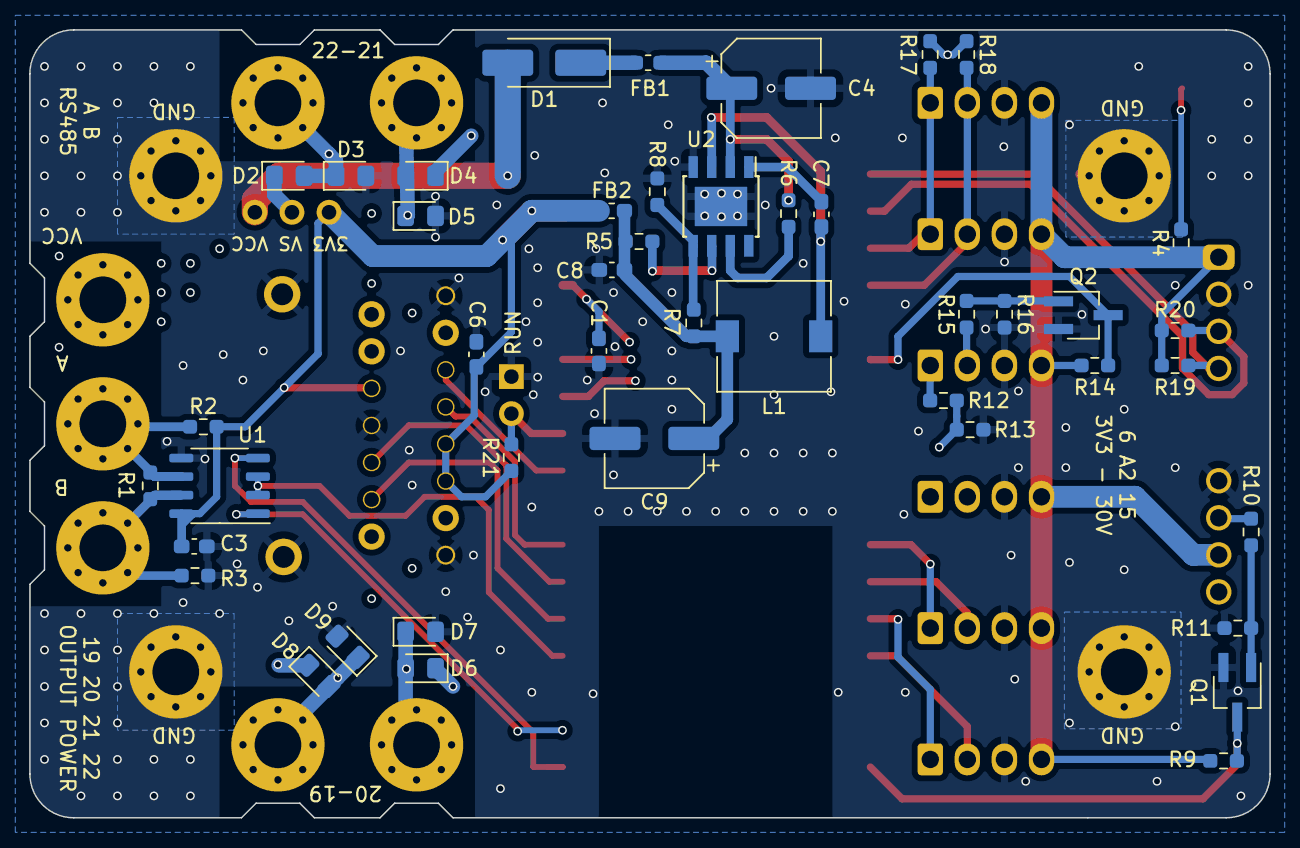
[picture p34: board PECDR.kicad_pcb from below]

Board: 4 copper layers, 85.0 x 54.0 mm, 68 parts (44 on the bottom side), 45 nets.

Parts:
C1: 10pF; C_0603_1608Metric_Pad1.08x0.95mm_HandSolder
C3, C6, C7, C8: 100nF; C_0603_1608Metric_Pad1.08x0.95mm_HandSolder
C4: 100uF 25V; CP_Elec_6.3x7.7
C9: 100uF 6V3; CP_Elec_6.3x7.7
D1: B340A; D_SMA_Handsoldering
D2, D3, D4, D5, D6, D7, D8, D9: B340A; D_0805_2012Metric_Pad1.15x1.40mm_HandSolder
D10: IHM; LED_0805_2012Metric_Pad1.15x1.40mm_HandSolder
FB1, FB2: Ferrite; L_0603_1608Metric_Pad1.05x0.95mm_HandSolder
J1: O2; MountingHole_3.2mm_M3_Pad_Via
J2: O4; MountingHole_3.2mm_M3_Pad_Via
J3: O1; MountingHole_3.2mm_M3_Pad_Via
J4: VCC; MountingHole_3.2mm_M3_Pad_Via
J5, J6: GP-I2C0; Molex_KK-254_AE-6410-04A_1x04_P2.54mm_Vertical
J7: GP-IN1; Molex_KK-254_AE-6410-04A_1x04_P2.54mm_Vertical
J8: GP/IN-ADC; Molex_KK-254_AE-6410-04A_1x04_P2.54mm_Vertical
J9: GP-ADC; Molex_KK-254_AE-6410-04A_1x04_P2.54mm_Vertical
J10, J11: GP-SPI; Molex_KK-254_AE-6410-04A_1x04_P2.54mm_Vertical
J12: O3; MountingHole_3.2mm_M3_Pad_Via
J13, J13#2, J13#3, J13#4: GND; MountingHole_3.2mm_M3_Pad_Via
J14: A; MountingHole_3.2mm_M3_Pad_Via
J15: B; MountingHole_3.2mm_M3_Pad_Via
J16: VS-SELECT; PinSocket_1x03_P2.54mm_Vertical
J17: GP-I2C1; Molex_KK-254_AE-6410-04A_1x04_P2.54mm_Vertical
JP1: RUM; PinSocket_1x02_P2.54mm_Vertical
L1: 10uH; L_Wuerth_WE-PD-Typ-M-Typ-S
Q1, Q2: BC848ALT1; SOT-23W_Handsoldering
R1: 4k7; R_0603_1608Metric_Pad0.98x0.95mm_HandSolder
R2, R3: 4K7; R_0603_1608Metric_Pad0.98x0.95mm_HandSolder
R4: 1K; R_0603_1608Metric_Pad0.98x0.95mm_HandSolder
R5, R17, R18, R19, R20, R21: 10k; R_0603_1608Metric_Pad0.98x0.95mm_HandSolder
R6: 100k; R_0603_1608Metric_Pad0.98x0.95mm_HandSolder
R7: 26k1 1%; R_0603_1608Metric_Pad0.98x0.95mm_HandSolder
R8: 10k 1%; R_0603_1608Metric_Pad0.98x0.95mm_HandSolder
R9, R10, R11, R12, R13, R14, R15, R16: 10K; R_0603_1608Metric_Pad0.98x0.95mm_HandSolder
U1: MAX485CSA+; SOP-8_3.9x4.9mm_P1.27mm
U2: FR9889; Diodes_PSOP-8
U3: RPI-PICO; RPI-PICO-SMD
U5: L298N; SINK-L298N

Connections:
+3V3: C3.1, C6.1, FB2.2, J5.4, J6.4, J7.2, J8.4, J9.4, J10.4, J11.4, J16.1, J17.4, R2.1, R4.1, R9.1, R14.1, R17.1, R18.1, R19.1, R20.1, R21.1, U1.8 (VCC), U3.36 (3V3), U5.6 (EnA), U5.9 (Vss), U5.11 (EnB)
/A: J14.1, R1.1, R2.2, U1.6 (A)
/ADC2: J8.1, R12.1
/B: J15.1, R1.2, R3.1, U1.7 (B)
/DriverInput: U1.4 (DI), U3.21 (GP16)
/G15: Q1.3 (C), R9.2, U3.20 (GP15)
/GP6: Q2.3 (C), R14.2, U3.9 (GP6)
/GP19: U3.25 (GP19), U5.12 (IN4)
/GP20: U3.26 (GP20), U5.10 (IN3)
/GP21: U3.27 (GP21), U5.7 (IN2)
/GP22: U3.29 (GP22), U5.5 (IN1)
/GP26-ADC0-SDA1: J9.1, U3.31 (GP26)
/GP27-ADC1-SCL1: J9.2, U3.32 (GP27)
/GP28-ADC2: C1.1, R12.2, R13.1, U3.34 (GP28)
/IN1: J7.3, R10.1
/IN2: J8.2, R15.1
/InputOutputEnable: U1.2 (~RE), U1.3 (DE), U3.24 (GP18)
/OUT1: D2.2 (A), D3.1 (K), J3.1, U5.2 (OUT1)
/OUT2: D4.2 (A), D5.1 (K), J1.1, U5.3 (OUT2)
/OUT3: D6.2 (A), D7.1 (K), J12.1, U5.13 (OUT3)
/OUT4: D8.2 (A), D9.1 (K), J2.1, U5.14 (OUT4)
/RUN: JP1.2 (B), R21.2, U3.30 (RUN)
/RXD0-SCL0-CS1-GP13: J11.2, U3.17 (GP13)
/RXD1-SCL0-CS0-GP5: J5.2, J6.2, R18.2, U3.7 (GP5_SCL0)
/ReceiverOutput: U1.1 (RO), U3.22 (GP17)
/SCL1-TX0-GP3: J17.2, R20.2, U3.5 (GP3)
/SCL1-TX1-GP11: J10.2, U3.15 (GP11)
/SDA1-SCK0-GP2: J17.1, R19.2, U3.4 (GP2)
/SDA1-SCK1-GP10: J10.1, U3.14 (GP10)
/TXD0-SDA0-RX1-GP12: J11.1, U3.16 (GP12)
/TXD1-SDA0-RX0-GP4: J5.1, J6.1, R17.2, U3.6 (GP4_SDA0)
GND: C1.2, C3.2, C4.2, C6.2, C8.2, C9.2, D3.2 (A), D5.2 (A), D7.2 (A), D9.2 (A), D10.1 (K), J5.3, J6.3, J7.4, J8.3, J9.3, J10.3, J11.3, J13.1, J13#2.1, J13#3.1, J13#4.1, J17.3, JP1.1 (A), Q1.2 (E), Q2.2 (E), R3.2, R8.1, R11.2, R13.2, R16.2, U1.5 (GND), U2.4 (GND), U2.9 (GND_TAP), U3.3 (GND), U3.8 (GND), U3.13 (GND), U3.18 (GND), U3.23 (GND), U3.28 (GND), U3.33 (GND), U3.35 (ADC_VREF), U3.37 (3V3_EN), U3.38 (GND), U5.1 (SENSE_A), U5.8 (GND), U5.15 (SENSE_B)
unnamed: C8.1, C9.1, FB2.1, L1.2, R5.2, R7.2
unnamed: D1.1 (K), FB1.2
unnamed: D10.2 (A), R4.2
unnamed: Q1.1 (B), R10.2, R11.1
unnamed: Q2.1 (B), R15.2, R16.1
unnamed: C7.2, U2.1 (BST)
unnamed: R7.1, R8.2, U2.5 (FB)
unnamed: C7.1, L1.1, U2.3 (LX)
unnamed: R5.1, U2.6 (PG)
unnamed: C4.1, FB1.1, R6.1, U2.2 (VIN)
unnamed: R6.2, U2.7 (~SHDN)
VCC: D1.2 (A), J4.1, J16.3
VS: D2.1 (K), D4.1 (K), D6.1 (K), D8.1 (K), J16.2, U5.4 (Vs)

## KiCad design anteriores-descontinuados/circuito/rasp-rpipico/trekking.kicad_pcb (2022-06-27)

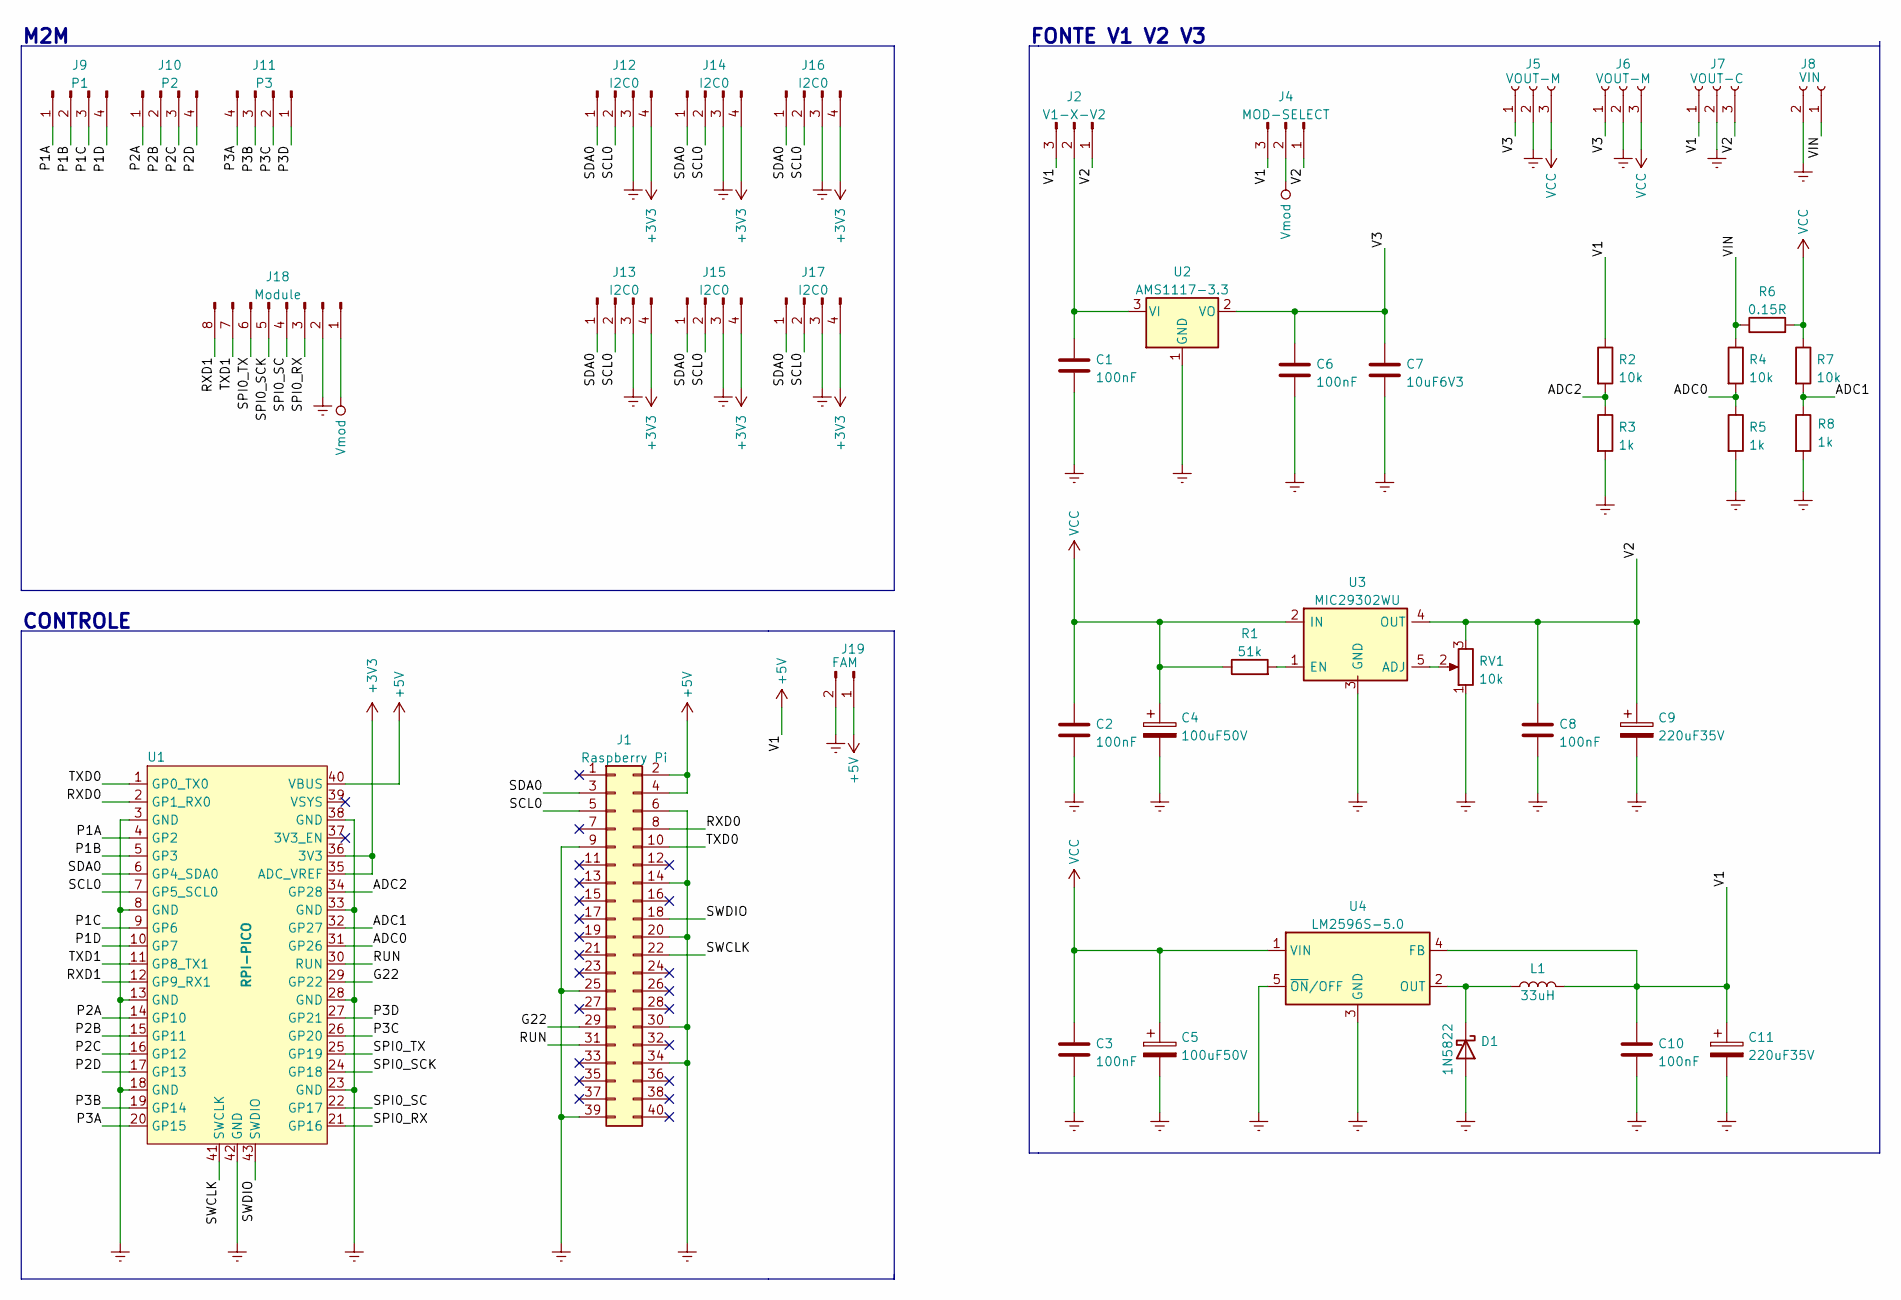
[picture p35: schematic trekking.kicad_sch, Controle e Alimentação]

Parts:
C1: 100nF
C2, C3, C6, C8, C10: 100nF; C_0805_2012Metric_Pad1.18x1.45mm_HandSolder
C4, C5: 100uF50V; CP_Elec_8x10
C7: 10uF6V3; C_0805_2012Metric_Pad1.18x1.45mm_HandSolder
C9, C11: 220uF35V; CP_Elec_8x10
D1: 1N5822; D_3220_8050Metric_Pad2.65x5.15mm_HandSolder
J1: Raspberry Pi; PinHeader_2x20_P2.54mm_Vertical
J2: V1-X-V2; PinHeader_1x03_P2.54mm_Vertical
J4: MOD-SELECT; PinHeader_1x03_P2.54mm_Vertical
J5, J6: VOUT-M; CONN5mm-3
J7: VOUT-C; CONN5mm-3
J8: VIN; AK300-2
J9: P1; Molex_KK-254_AE-6410-04A_1x04_P2.54mm_Vertical
J10: P2; Molex_KK-254_AE-6410-04A_1x04_P2.54mm_Vertical
J11: P3; Molex_KK-254_AE-6410-04A_1x04_P2.54mm_Vertical
J12, J13, J14, J15, J16, J17: I2C0; Molex_KK-254_AE-6410-04A_1x04_P2.54mm_Vertical
J18: Module; PinHeader_1x08_P2.54mm_Vertical
J19: FAM; PinHeader_1x02_P2.54mm_Vertical
L1: 33uH; L_12x12mm_H8mm
R1: 51k; R_0805_2012Metric_Pad1.20x1.40mm_HandSolder
R2, R4, R7: 10k; R_0805_2012Metric_Pad1.20x1.40mm_HandSolder
R3, R5, R8: 1k; R_0805_2012Metric_Pad1.20x1.40mm_HandSolder
R6: 0.15R; R_2512_6332Metric_Pad1.40x3.35mm_HandSolder
RV1: 10k; Potentiometer_Bourns_3266Y_Vertical
U1: RPI-PICO; RPI-PICO-SMD
U2: AMS1117-3.3; SOT-223-3_TabPin2
U3: MIC29302WU; TO-263-5_TabPin3
U4: LM2596S-5.0; TO-263-5_TabPin3

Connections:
+3V3: J12.4, J13.4, J14.4, J15.4, J16.4, J17.4, U1.35 (ADC_VREF), U1.36 (3V3)
+5V: C10.1, C11.1, J1.2, J1.4, J2.3, J4.3, J7.1, J19.1, L1.2, R2.1, U1.40 (VBUS), U4.4 (FB)
/ADC0: R4.2, R5.1, U1.31 (GP26)
/ADC1: R7.2, R8.1, U1.32 (GP27)
/ADC2: R2.2, R3.1, U1.34 (GP28)
/G22: J1.29, U1.29 (GP22)
/P1A: J9.1, U1.4 (GP2)
/P1B: J9.2, U1.5 (GP3)
/P1C: J9.3, U1.9 (GP6)
/P1D: J9.4, U1.10 (GP7)
/P2A: J10.1, U1.14 (GP10)
/P2B: J10.2, U1.15 (GP11)
/P2C: J10.3, U1.16 (GP12)
/P2D: J10.4, U1.17 (GP13)
/P3A: J11.4, U1.20 (GP15)
/P3B: J11.3, U1.19 (GP14)
/P3C: J11.2, U1.26 (GP20)
/P3D: J11.1, U1.27 (GP21)
/RUN: J1.31, U1.30 (RUN)
/RXD0: J1.8, U1.2 (GP1_RX0)
/RXD1: J18.8, U1.12 (GP9_RX1)
/SCL0: J1.5, J12.2, J13.2, J14.2, J15.2, J16.2, J17.2, U1.7 (GP5_SCL0)
/SDA0: J1.3, J12.1, J13.1, J14.1, J15.1, J16.1, J17.1, U1.6 (GP4_SDA0)
/SPI0_RX: J18.3, U1.21 (GP16)
/SPI0_SC: J18.4, U1.22 (GP17)
/SPI0_SCK: J18.5, U1.24 (GP18)
/SPI0_TX: J18.6, U1.25 (GP19)
/SWCLK: J1.22, U1.41 (SWCLK)
/SWDIO: J1.18, U1.43 (SWDIO)
/TXD0: J1.10, U1.1 (GP0_TX0)
/TXD1: J18.7, U1.11 (GP8_TX1)
/V2: C8.1, C9.1, J2.1, J4.1, J7.3, RV1.3, U3.4 (OUT); also elsewhere on the board
/V3: C6.1, C7.1, J5.1, J6.1, U2.2 (VO)
/VIN: J8.1, R4.1, R6.1
Earth: C1.2, C2.2, C3.2, C4.2, C5.2, C6.2, C7.2, C8.2, C9.2, C10.2, C11.2, D1.2 (A), J1.6, J1.9, J1.14, J1.20, J1.25, J1.30, J1.34, J1.39, J5.2, J6.2, J7.2, J8.2, J12.3, J13.3, J14.3, J15.3, J16.3, J17.3, J18.2, J19.2, R3.2, R5.2, R8.2, RV1.1, U1.3 (GND), U1.8 (GND), U1.13 (GND), U1.18 (GND), U1.23 (GND), U1.28 (GND), U1.33 (GND), U1.38 (GND), U1.42 (GND), U2.1 (GND), U3.3 (GND), U4.3 (GND), U4.5 (~ON/OFF)
unnamed: C1.1, J2.2, U2.3 (VI)
unnamed: D1.1 (K), L1.1, U4.2 (OUT)
unnamed: R1.2, U3.1 (EN)
unnamed: RV1.2, U3.5 (ADJ)
VCC: C2.1, C3.1, C4.1, C5.1, J5.3, J6.3, R1.1, R6.2, R7.1, U3.2 (IN), U4.1 (VIN)
Vmod: J4.2, J18.1

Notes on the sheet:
CONTROLE
M2M
FONTE V1 V2 V3

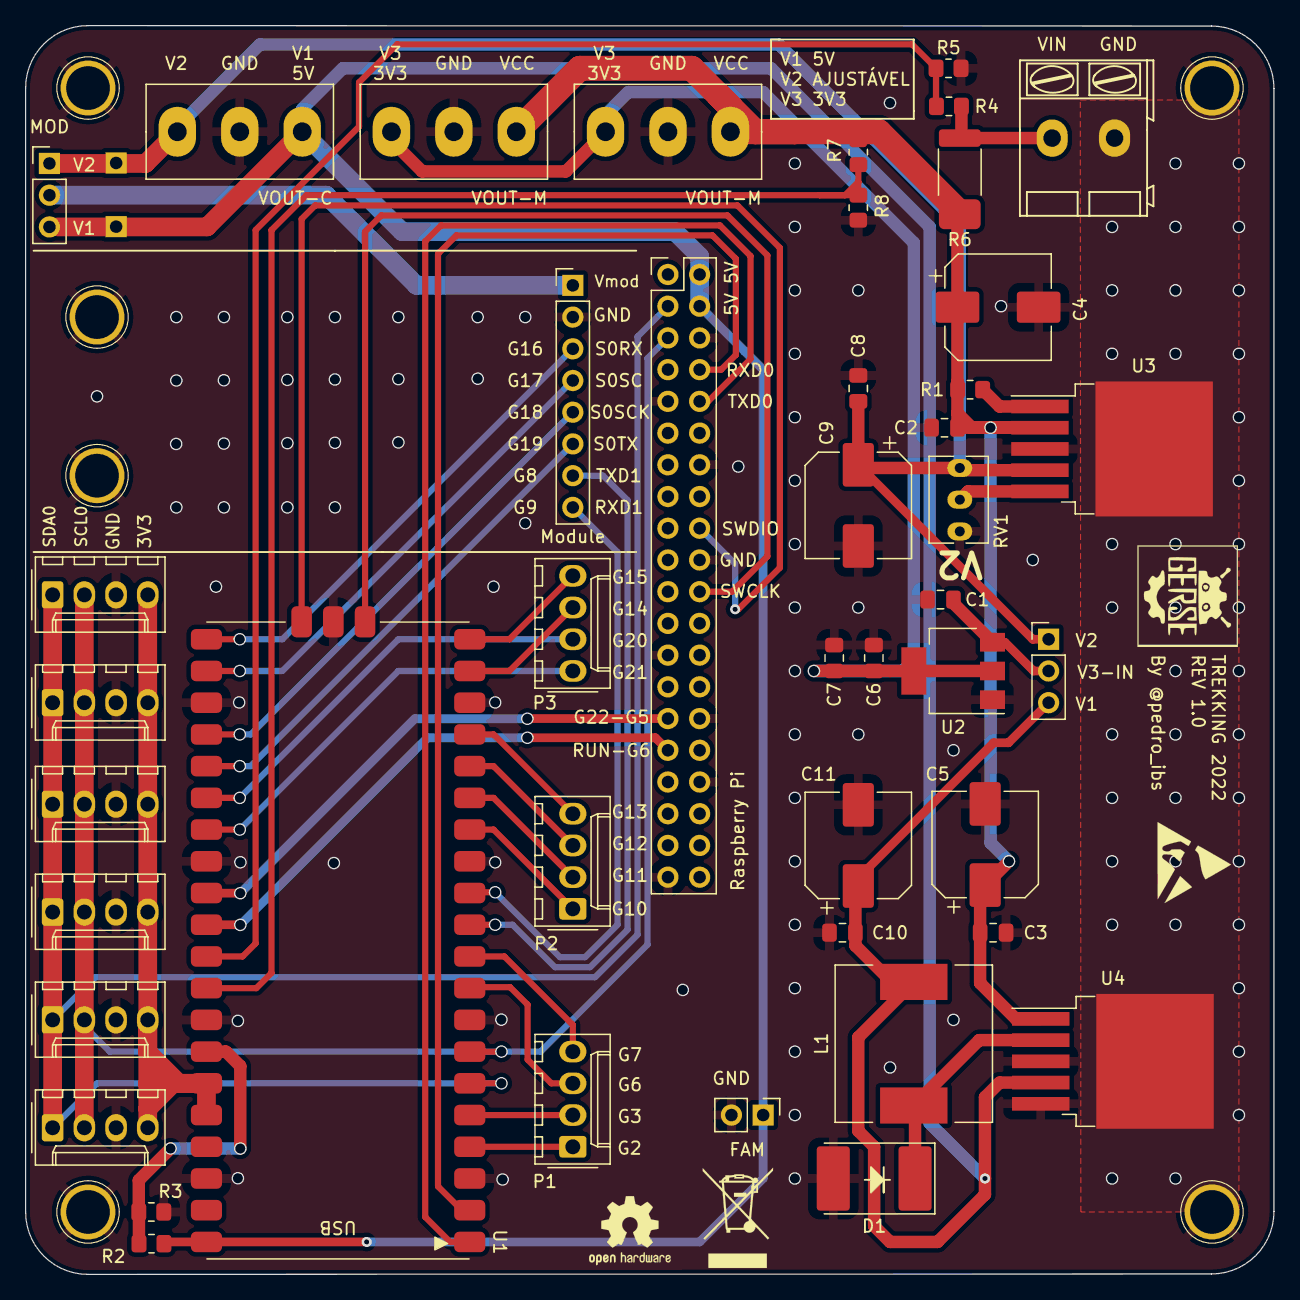
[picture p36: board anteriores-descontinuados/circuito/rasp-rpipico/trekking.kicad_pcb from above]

Board: 2 copper layers, 100.0 x 100.0 mm, 45 parts (0 on the bottom side), 41 nets.

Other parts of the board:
J**: HOLE

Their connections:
/V2: J**.1; also elsewhere on the board

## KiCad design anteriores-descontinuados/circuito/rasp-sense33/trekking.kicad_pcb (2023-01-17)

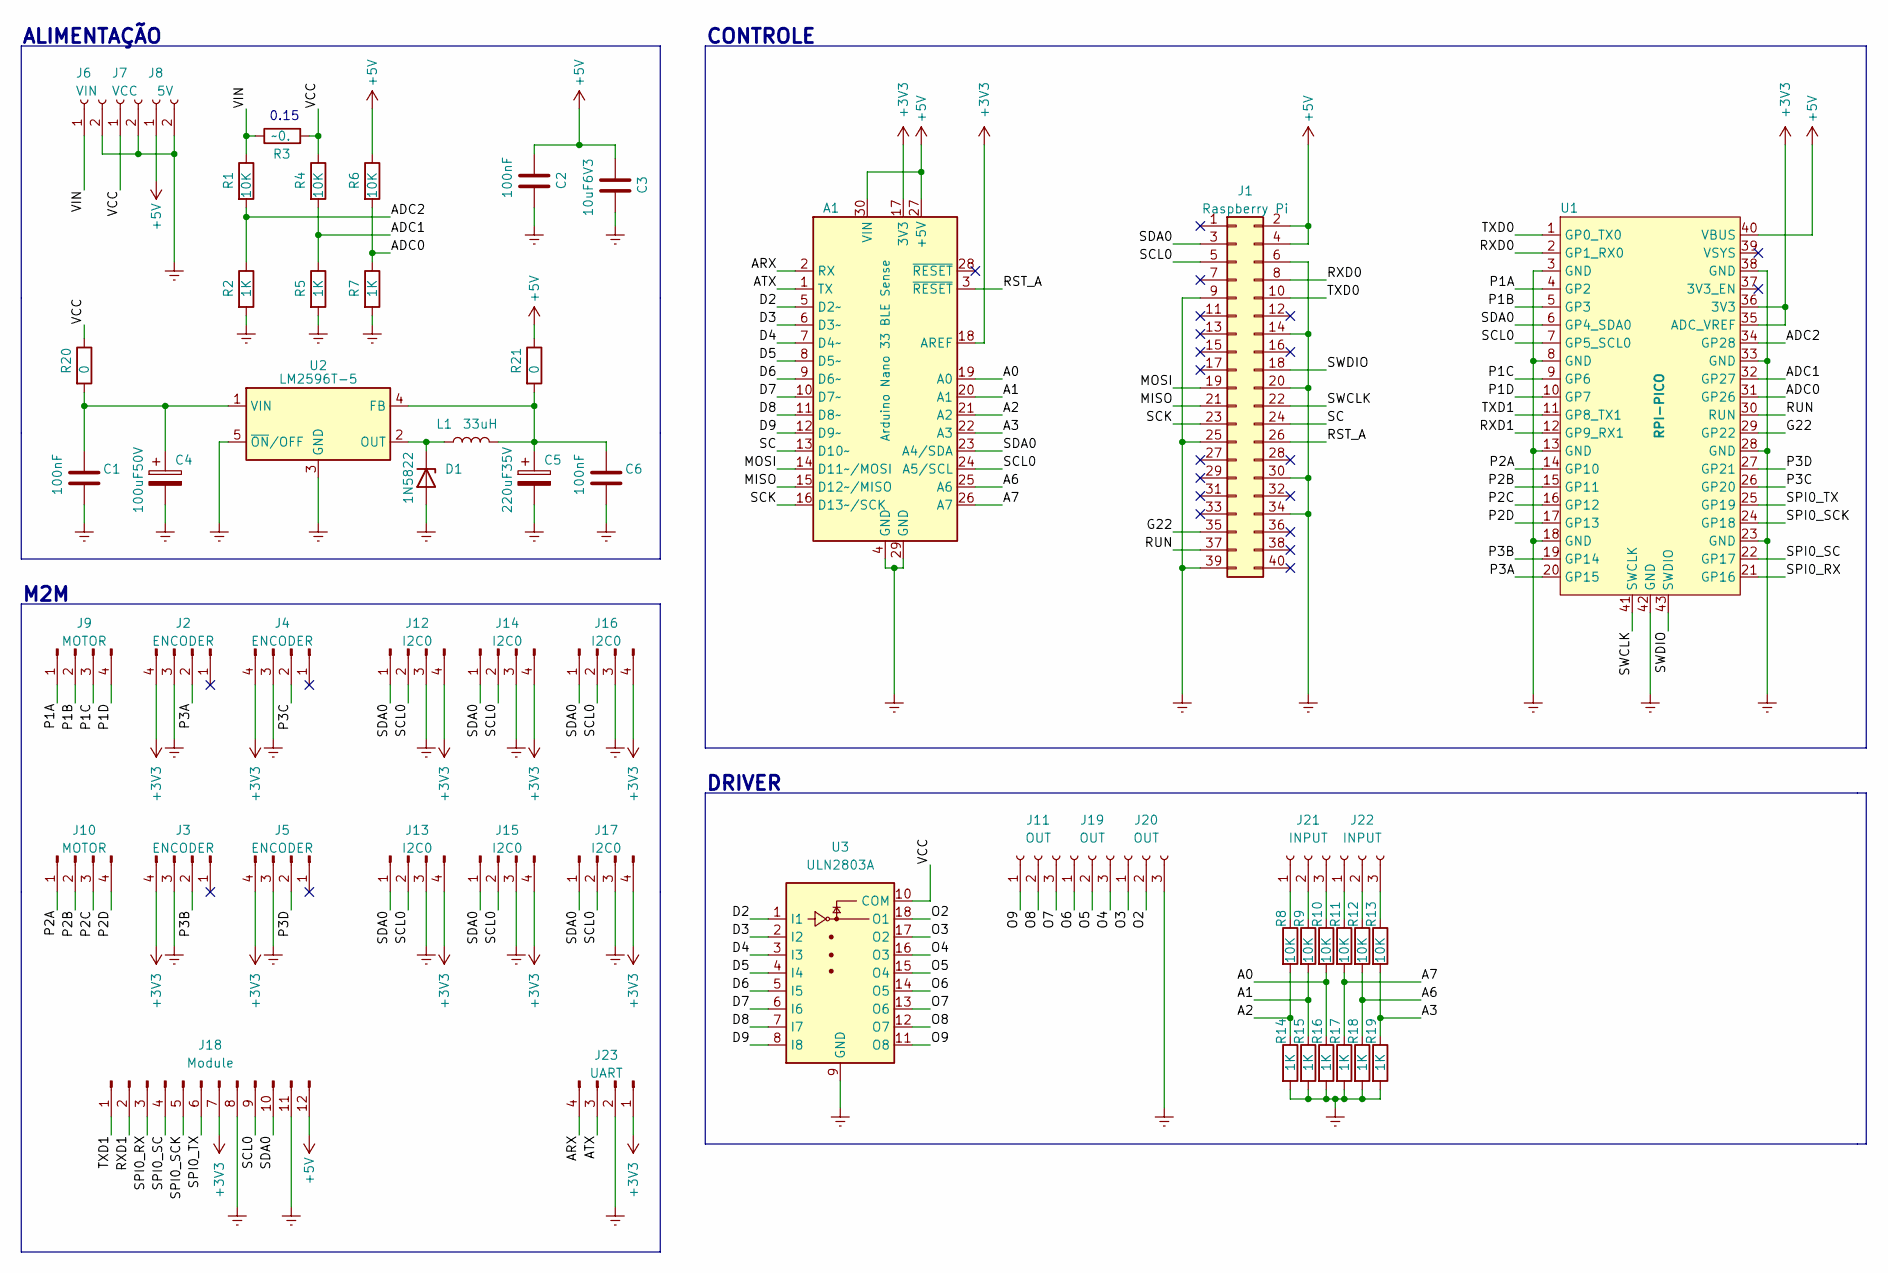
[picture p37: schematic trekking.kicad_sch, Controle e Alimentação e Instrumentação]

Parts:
A1: Arduino Nano 33 BLE Sense; Arduino_Nano
C1, C2, C6: 100nF; C_0805_2012Metric_Pad1.18x1.45mm_HandSolder
C3: 10uF6V3; C_0805_2012Metric_Pad1.18x1.45mm_HandSolder
C4: 100uF50V; CP_Elec_8x10
C5: 220uF35V; CP_Elec_8x10
D1: 1N5822; My_D_MELF-RM10_Universal_Handsoldering_2
J1: Raspberry Pi; PinHeader_2x20_P2.54mm_Vertical
J2, J3, J4, J5: ENCODER; Molex_KK-254_AE-6410-04A_1x04_P2.54mm_Vertical
J6: VIN; AK300-2
J7: VCC; AK300-2
J8: 5V; AK300-2
J9, J10: MOTOR; Molex_KK-254_AE-6410-04A_1x04_P2.54mm_Vertical
J11, J19, J20: OUT; CONN5mm-3
J12, J13, J14, J15, J16, J17: I2C0; Molex_KK-254_AE-6410-04A_1x04_P2.54mm_Vertical
J18: Module; PinHeader_1x12_P2.54mm_Vertical
J21, J22: INPUT; CONN5mm-3
J23: UART; Molex_KK-254_AE-6410-04A_1x04_P2.54mm_Vertical
L1: 33uH; L_12x12mm_H8mm
R1, R4, R6, R8, R9, R10, R11, R12, R13: 10K; R_0805_2012Metric_Pad1.20x1.40mm_HandSolder
R2, R5, R7, R14, R15, R16, R17, R18, R19: 1K; R_0805_2012Metric_Pad1.20x1.40mm_HandSolder
R3: ~0.; R_1206_3216Metric_Pad1.30x1.75mm_HandSolder
R20, R21: 0; R_0805_2012Metric_Pad1.20x1.40mm_HandSolder
U1: RPI-PICO; RPI-PICO-SMD
U2: LM2596T-5; TO-263-5_TabPin3
U3: ULN2803A; SOIC-18W_7.5x11.6mm_P1.27mm

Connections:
+3V3: A1.17 (3V3), A1.18 (AREF), J2.4, J3.4, J4.4, J5.4, J12.4, J13.4, J14.4, J15.4, J16.4, J17.4, J18.7, J23.1, U1.35 (ADC_VREF), U1.36 (3V3)
+5V: A1.27 (+5V), A1.30 (VIN), C2.1, C3.1, J1.2, J1.4, J8.1, J18.12, R6.1, R21.1, U1.40 (VBUS)
/A0: A1.19 (A0), R10.2, R16.1
/A1: A1.20 (A1), R9.2, R15.1
/A2: A1.21 (A2), R8.2, R14.1
/A3: A1.22 (A3), R13.2, R19.1
/A6: A1.25 (A6), R12.2, R18.1
/A7: A1.26 (A7), R11.2, R17.1
/ADC0: R6.2, R7.1, U1.31 (GP26)
/ADC1: R4.2, R5.1, U1.32 (GP27)
/ADC2: R1.2, R2.1, U1.34 (GP28)
/ARX: A1.2 (RX), J23.4
/ATX: A1.1 (TX), J23.3
/D2: A1.5 (D2~), U3.1 (I1)
/D3: A1.6 (D3~), U3.2 (I2)
/D4: A1.7 (D4~), U3.3 (I3)
/D5: A1.8 (D5~), U3.4 (I4)
/D6: A1.9 (D6~), U3.5 (I5)
/D7: A1.10 (D7~), U3.6 (I6)
/D8: A1.11 (D8~), U3.7 (I7)
/D9: A1.12 (D9~), U3.8 (I8)
/G22: J1.35, U1.29 (GP22)
/MISO: A1.15 (D12~/MISO), J1.21
/MOSI: A1.14 (D11~/MOSI), J1.19
/O2: J20.2, U3.18 (O1)
/O3: J20.1, U3.17 (O2)
/O4: J19.3, U3.16 (O3)
/O5: J19.2, U3.15 (O4)
/O6: J19.1, U3.14 (O5)
/O7: J11.3, U3.13 (O6)
/O8: J11.2, U3.12 (O7)
/O9: J11.1, U3.11 (O8)
/P1A: J9.1, U1.4 (GP2)
/P1B: J9.2, U1.5 (GP3)
/P1C: J9.3, U1.9 (GP6)
/P1D: J9.4, U1.10 (GP7)
/P2A: J10.1, U1.14 (GP10)
/P2B: J10.2, U1.15 (GP11)
/P2C: J10.3, U1.16 (GP12)
/P2D: J10.4, U1.17 (GP13)
/P3A: J2.2, U1.20 (GP15)
/P3B: J3.2, U1.19 (GP14)
/P3C: J4.2, U1.26 (GP20)
/P3D: J5.2, U1.27 (GP21)
/RST_A: A1.3 (~RESET), J1.26
/RUN: J1.37, U1.30 (RUN)
/RXD0: J1.8, U1.2 (GP1_RX0)
/RXD1: J18.2, U1.12 (GP9_RX1)
/SC: A1.13 (D10~), J1.24
/SCK: A1.16 (D13~/SCK), J1.23
/SCL0: A1.24 (A5/SCL), J1.5, J12.2, J13.2, J14.2, J15.2, J16.2, J17.2, J18.9, U1.7 (GP5_SCL0)
/SDA0: A1.23 (A4/SDA), J1.3, J12.1, J13.1, J14.1, J15.1, J16.1, J17.1, J18.10, U1.6 (GP4_SDA0)
/SPI0_RX: J18.3, U1.21 (GP16)
/SPI0_SC: J18.4, U1.22 (GP17)
/SPI0_SCK: J18.5, U1.24 (GP18)
/SPI0_TX: J18.6, U1.25 (GP19)
/SWCLK: J1.22, U1.41 (SWCLK)
/SWDIO: J1.18, U1.43 (SWDIO)
/TXD0: J1.10, U1.1 (GP0_TX0)
/TXD1: J18.1, U1.11 (GP8_TX1)
/VCC: J7.1, R3.2, R4.1, R20.1, U3.10 (COM); also elsewhere on the board
/VIN: J6.1, R1.1, R3.1; also elsewhere on the board
Earth: A1.4 (GND), A1.29 (GND), C1.2, C2.2, C3.2, C4.2, C5.2, C6.2, D1.2 (A), J1.6, J1.9, J1.14, J1.20, J1.25, J1.30, J1.34, J1.39, J2.3, J3.3, J4.3, J5.3, J6.2, J7.2, J8.2, J12.3, J13.3, J14.3, J15.3, J16.3, J17.3, J18.8, J18.11, J20.3, J23.2, R2.2, R5.2, R7.2, R14.2, R15.2, R16.2, R17.2, R18.2, R19.2, U1.3 (GND), U1.8 (GND), U1.13 (GND), U1.18 (GND), U1.23 (GND), U1.28 (GND), U1.33 (GND), U1.38 (GND), U1.42 (GND), U2.3 (GND), U2.5 (~ON/OFF), U3.9 (GND)
unnamed: C1.1, C4.1, R20.2, U2.1 (VIN)
unnamed: C5.1, C6.1, L1.2, R21.2, U2.4 (FB)
unnamed: D1.1 (K), L1.1, U2.2 (OUT)
unnamed: J21.1, R8.1
unnamed: J21.2, R9.1
unnamed: J21.3, R10.1
unnamed: J22.1, R11.1
unnamed: J22.2, R12.1
unnamed: J22.3, R13.1

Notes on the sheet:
ALIMENTAÇÃO
CONTROLE
M2M
DRIVER
0.15

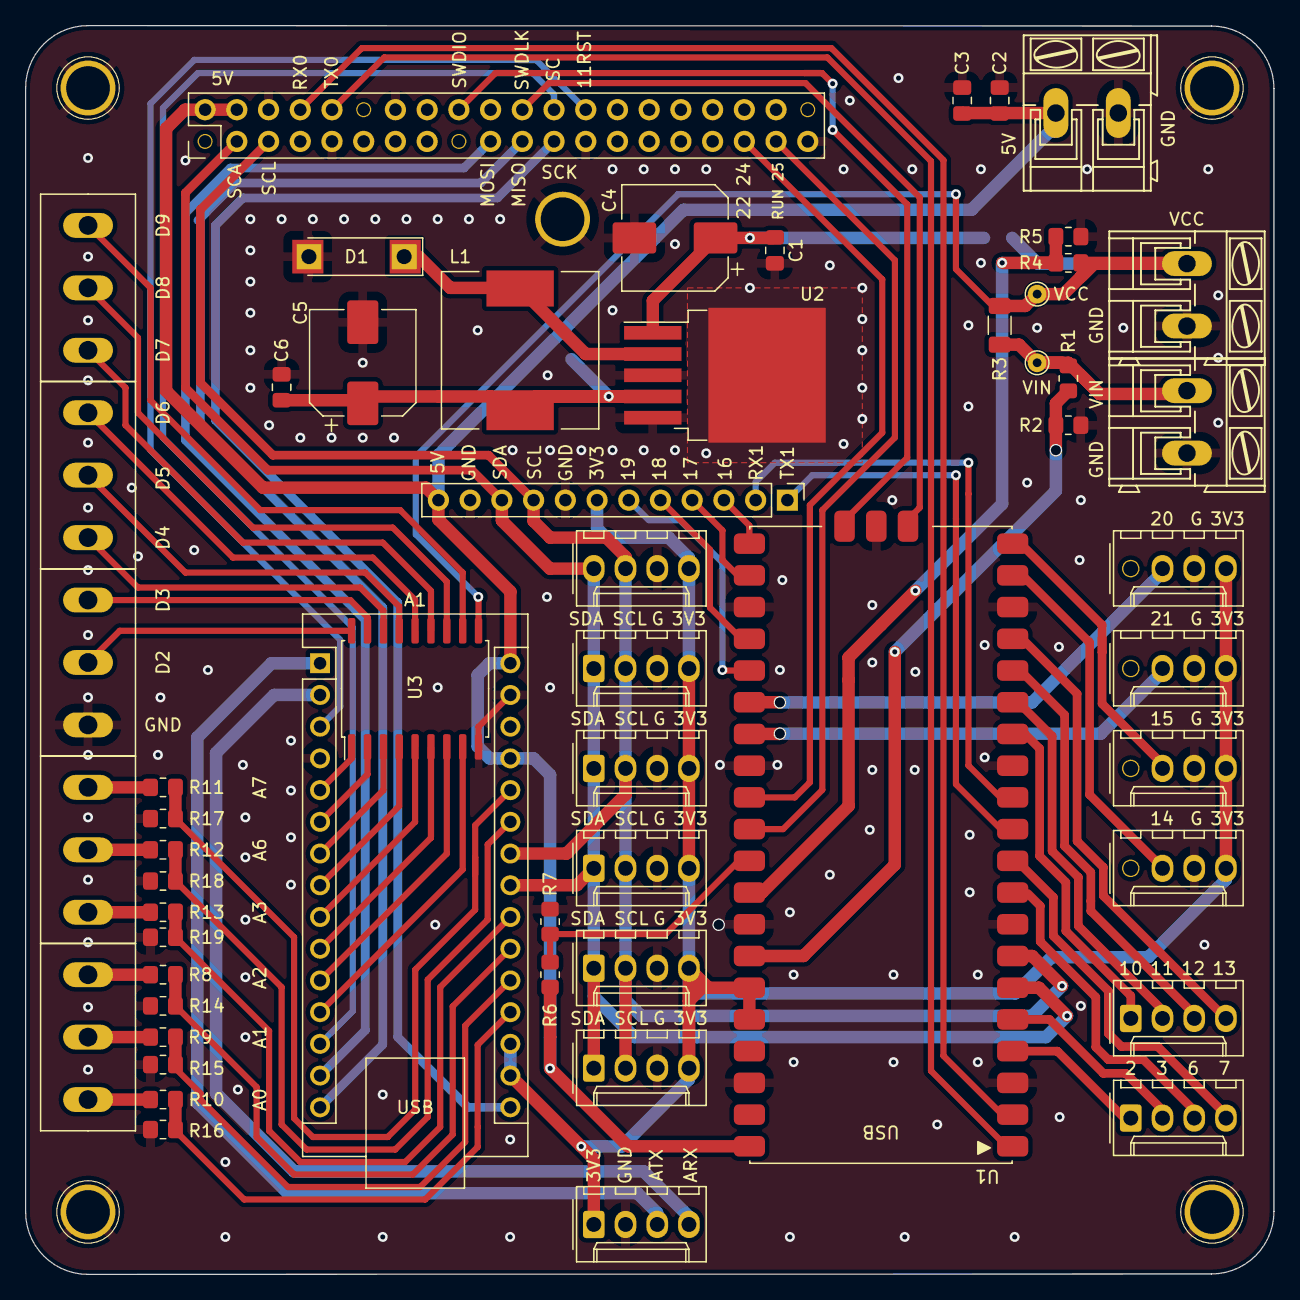
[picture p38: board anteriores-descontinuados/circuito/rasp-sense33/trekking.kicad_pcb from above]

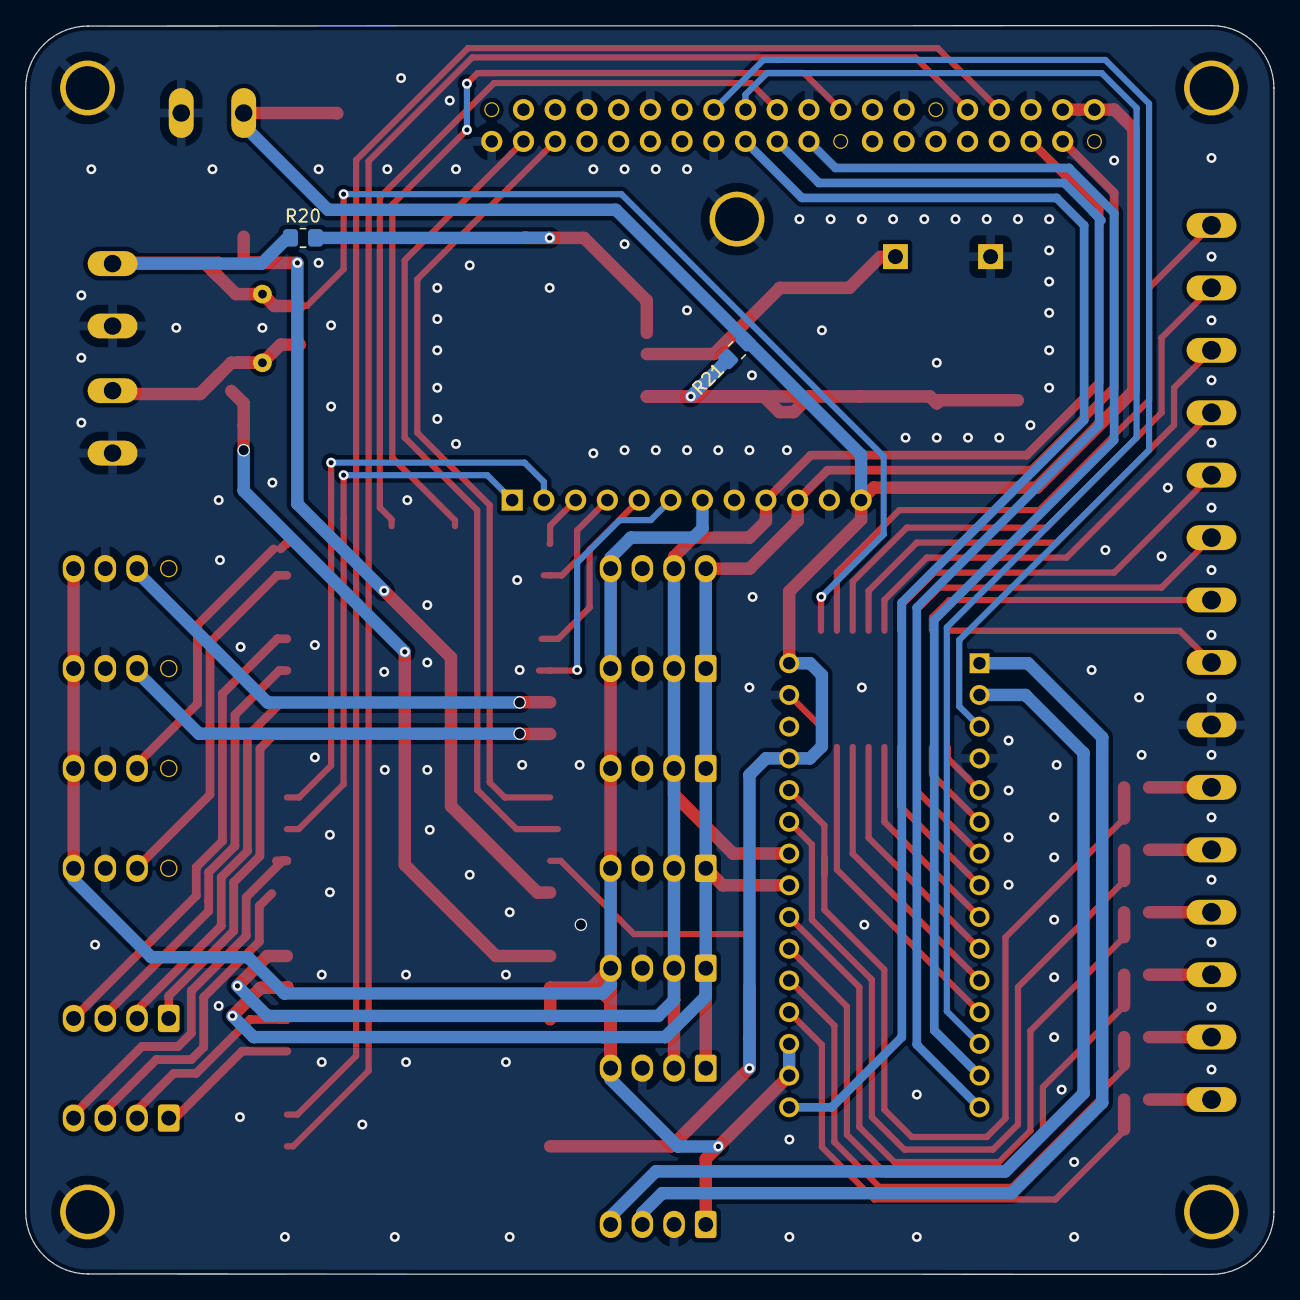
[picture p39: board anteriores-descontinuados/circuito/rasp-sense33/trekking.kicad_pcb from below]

Board: 2 copper layers, 100.0 x 100.0 mm, 58 parts (2 on the bottom side), 72 nets.

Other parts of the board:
VCC: TestPoint_THTPad_D1.5mm_Drill0.7mm
VIN: TestPoint_THTPad_D1.5mm_Drill0.7mm

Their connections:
/VCC: VCC.1; also elsewhere on the board
/VIN: VIN.1; also elsewhere on the board

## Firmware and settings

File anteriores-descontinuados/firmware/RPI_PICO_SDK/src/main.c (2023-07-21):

/**
 * simple_uart.c
 *
 *  @date Created at:	07/08/2022 10:50:05
 *	@author:	Pedro Igor B. S.
 *	@email:		pedro.igor.ifsp@gmail.com
 * 	GitHub:		https://github.com/pedro-ibs
 * 	tabSize:	8
 *
 * #######################################################################
 *   Copyright (C) Pedro Igor B. S 2021
 * -------------------------------------------------------------------
 *
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
 *
 * TODO: documentation or resume or Abstract
 *
 */



/* Includes ----------------------------------------------------------------------------------------------------------------------------------------------*/
#include <config.h>
#include <pico/multicore.h>
#include <pico/util/queue.h>
#include <simple_uart.h>
#include <textProtocol.h>
#include <motor.h> 
#include <pid.h>
#include <telemetry_power.h>
/* Setings -----------------------------------------------------------------------------------------------------------------------------------------------*/
/* Setup -------------------------------------------------------------------------------------------------------------------------------------------------*/
typedef struct {
	motor right1;
	motor right2;
	motor left1;
	motor left2;
	
} dataMotors;

typedef struct  {
	int motorRight1;
	int motorRight2;
	int motorLeft1;
	int motorLeft2;
} setpoint;



typedef struct {
	pid motorRight1;
	pid motorRight2;
	pid motorLeft1;
	pid motorLeft2;
} dataPIDs;

queue_t sendToCore0Queue;
queue_t sendToCore1Queue;

static float fGlobalPowerSupplyA	= 0.00;
static float fGlobalPowerSupplyB	= 0.00;
static float fGlobalPowerSystem		= 0.00;


/* Function prototype ------------------------------------------------------------------------------------------------------------------------------------*/
void main_showInformation(const dataMotors *motors, char *buffer);
void core1_entry( void );
/* -------------------------------------------------------------------------------------------------------------------------------------------------------*/

/**
 * @brief the main is pined at core 0, this core are dedicated to communication between devices
 * both queue be pinned at core 0 too, so, send and receive queue there are in "function main"
 * perspective 
 */
int main( void ) {

	char buffer[ CONFIG_BUFFER_SIZE ]	= { 0		};
	setpoint velocities			= { 0, 0, 0, 0	};
	dataMotors motors			= { 0		};

	float fPowerSupplyA			= 0.00;
	float fPowerSupplyB			= 0.00;
	float fPowerSystem			= 0.00;
	uint count				= 0;

	/* base setup */
	stdio_init_all();
	uart_vSetup( _idxUart0, CONFIG_BAUD_RATE_UART0, HARDWARE_TX0_GPIO, HARDWARE_RX0_GPIO );
	uart_vSetup( _idxUart1, CONFIG_BAUD_RATE_UART0, HARDWARE_TX1_GPIO, HARDWARE_RX1_GPIO );

	telemetry_vSetup();

	/* multicore setup */
	queue_init( &sendToCore1Queue,	sizeof( setpoint	), CONFIG_QUEUE_ELEMENTS );
    	queue_init( &sendToCore0Queue,	sizeof( dataMotors	), CONFIG_QUEUE_ELEMENTS );
	multicore_launch_core1( core1_entry );

	/* set the first setpoint at core 1 */
	queue_add_blocking( &sendToCore1Queue, &velocities );

	/* show the first data */
	queue_remove_blocking( &sendToCore0Queue, &motors );
	textp_puCleanBlk( ( uint8_t* )buffer, CONFIG_BUFFER_SIZE );
	main_showInformation( &motors, buffer );


	while (true) {

		const char *pcBuffer = uart_pcGetBuffer( _idxUart0 );

		if ( textp_bFindString( pcBuffer, "\n" ) == true ) {

			if( textp_bGetLabelInfo( pcBuffer, "mr1", 0, buffer ) ){ 
				velocities.motorRight1	= atoi(buffer);
			}

			if( textp_bGetLabelInfo( pcBuffer, "mr2", 0, buffer ) ){
				velocities.motorRight2	= atoi(buffer);
			}

			if( textp_bGetLabelInfo( pcBuffer, "ml1", 0, buffer ) ){
				velocities.motorLeft1	= atoi(buffer);
			}

			if( textp_bGetLabelInfo( pcBuffer, "ml2", 0, buffer ) ){
				velocities.motorLeft2	= atoi(buffer);
			}

			queue_add_blocking( &sendToCore1Queue, &velocities );

			uart_vCleanBuffer( _idxUart0 );
		}


		if( queue_try_remove( &sendToCore0Queue, &motors ) == true ){
			textp_puCleanBlk( (uint8_t*)buffer, CONFIG_BUFFER_SIZE );
			main_showInformation( &motors, buffer );
		}


		count++;

		if (  count >= CONFIG_MOVING_AVERAGE ){

			fGlobalPowerSupplyA	= ( fPowerSupplyA	/ CONFIG_MOVING_AVERAGE ) + CONFIG_POWER_SUPPLY_OFFSET;
			fGlobalPowerSupplyB	= ( fPowerSupplyB	/ CONFIG_MOVING_AVERAGE ) + CONFIG_POWER_SUPPLY_OFFSET;
			fGlobalPowerSystem	= ( fPowerSystem	/ CONFIG_MOVING_AVERAGE ) + CONFIG_POWER_SYSTEM_OFFSET;
			
			fPowerSupplyA		= 0;
			fPowerSupplyB		= 0;
			fPowerSystem		= 0;

			count			= 0;

		} else {
			fPowerSupplyA		= fPowerSupplyA	+ telemetry_fGetPowerSupplyA();
			fPowerSupplyB		= fPowerSupplyB	+ telemetry_fGetPowerSupplyB();
			fPowerSystem		= fPowerSystem	+ telemetry_fGetPowerSystem();
		}

		sleep_ms( CONFIG_DELAY_LOOP_MS );

	}
}



void core1_entry( void )   {
	
	setpoint velocities = {0, 0, 0, 0};

	dataMotors motors = {
		.right1		= { HARDWARE_M1CHA_GPIO, HARDWARE_M1CHB_GPIO, 0, 0		},
		.right2		= { HARDWARE_M2CHA_GPIO, HARDWARE_M2CHB_GPIO, 0, 0		},
		.left1		= { HARDWARE_M4CHA_GPIO, HARDWARE_M4CHB_GPIO, 0, 0		},
		.left2		= { HARDWARE_M3CHA_GPIO, HARDWARE_M3CHB_GPIO, 0, 0		},
	};

	dataPIDs pids = {
		.motorRight1	= { CONFIG_KP, CONFIG_KI, CONFIG_KD, 0, 0, 0, 0, 0, 0, 0, 0, 0 	},
		.motorRight2	= { CONFIG_KP, CONFIG_KI, CONFIG_KD, 0, 0, 0, 0, 0, 0, 0, 0, 0 	},
		.motorLeft1	= { CONFIG_KP, CONFIG_KI, CONFIG_KD, 0, 0, 0, 0, 0, 0, 0, 0, 0 	},
		.motorLeft2	= { CONFIG_KP, CONFIG_KI, CONFIG_KD, 0, 0, 0, 0, 0, 0, 0, 0, 0 	}
	};


	motor_vSetup(&motors.right1,	CONFIG_PWM_FREQUENCY_HZ, CONFIG_PWM_DUTY_CYCLE_START);
	motor_vSetup(&motors.right2,	CONFIG_PWM_FREQUENCY_HZ, CONFIG_PWM_DUTY_CYCLE_START);
	motor_vSetup(&motors.left1,	CONFIG_PWM_FREQUENCY_HZ, CONFIG_PWM_DUTY_CYCLE_START);
	motor_vSetup(&motors.left2,	CONFIG_PWM_FREQUENCY_HZ, CONFIG_PWM_DUTY_CYCLE_START);


	queue_remove_blocking( &sendToCore1Queue, &velocities );

	// pids.motorRight1.fSetPoint	= velocities.motorRight1;
	// pids.motorRight2.fSetPoint	= velocities.motorRight2;
	// pids.motorLeft1.fSetPoint	= velocities.motorLeft1;
	// pids.motorLeft2.fSetPoint	= velocities.motorLeft2;

	motors.right1.pwm	= velocities.motorRight1;
	motors.right2.pwm	= velocities.motorRight2;
	motors.left1.pwm	= velocities.motorLeft1;
	motors.left2.pwm	= velocities.motorLeft2;

	while (true) {

		queue_try_add(&sendToCore0Queue, &motors);

		if( queue_try_remove(&sendToCore1Queue, &velocities) == true ){
			// pids.motorRight1.fSetPoint	= velocities.motorRight1;
			// pids.motorRight2.fSetPoint	= velocities.motorRight2;
			// pids.motorLeft1.fSetPoint	= velocities.motorLeft1;
			// pids.motorLeft2.fSetPoint	= velocities.motorLeft2;
		}

		motor_vMove(&motors.right1,	velocities.motorRight1	); 
		motor_vMove(&motors.right2,	velocities.motorRight2	); 
		motor_vMove(&motors.left1,	velocities.motorLeft1	); 
		motor_vMove(&motors.left2,	velocities.motorLeft2	); 

		
		sleep_ms( CONFIG_PID_FRAME_HATE_MS );		
	}

}

void main_showInformation( const dataMotors *motors, char *buffer ){

	sprintf( buffer, CONFIG_JSON,
		motors->left1.pwm,
		motors->left1.pwm_max,
		0.0,

		motors->left2.pwm,
		motors->left2.pwm_max,
		0.0,

		motors->right1.pwm,
		motors->right1.pwm_max,
		0.0,

		motors->right2.pwm,
		motors->right2.pwm_max,
		0.0,

		fGlobalPowerSupplyA,
		fGlobalPowerSupplyB,
		fGlobalPowerSystem
	);

	uart_vSendStringLn(_idxUart0, buffer);
	uart_vSendStringLn(_idxUart1, buffer);

}

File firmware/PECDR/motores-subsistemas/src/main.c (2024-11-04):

/**
 * simple_uart.c
 *
 *  @date Created at:	07/08/2022 10:50:05
 *	@author:	Pedro Igor B. S.
 *	@email:		pedro.igor.ifsp@gmail.com
 * 	GitHub:		https://github.com/pedro-ibs
 * 	tabSize:	8
 *
 * #######################################################################
 *   Copyright (C) Pedro Igor B. S 2021
 * -------------------------------------------------------------------
 *
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
 *
 * TODO: documentation or resume or Abstract
 *
 */



/* Includes ----------------------------------------------------------------------------------------------------------------------------------------------*/
#include <pico/stdlib.h>
#include <pico/multicore.h>
#include <pico/util/queue.h>

#include <textProtocol.h>
#include <config.h>
#include <rs485.h>
#include <servo.h>
#include <motor.h>
#include <pid.h>

/* Setings -----------------------------------------------------------------------------------------------------------------------------------------------*/
queue_t sendToCore1Queue;
/* Setup -------------------------------------------------------------------------------------------------------------------------------------------------*/
/* Function prototype ------------------------------------------------------------------------------------------------------------------------------------*/
void core1_entry( void );
/* -------------------------------------------------------------------------------------------------------------------------------------------------------*/

typedef enum {
	_Stop =0,
	_Front,
	_Back,
} Direction ;

typedef struct  {
	
	float		velocity;
	Direction	direction;

} Motor;


int main( void ) {


	/* base setup */
	stdio_init_all();

	gpio_init	( HARDWARE_LED_GPIO				);
	gpio_set_dir	( HARDWARE_LED_GPIO,		GPIO_OUT	);

	rs485_vSetup( CONFIG_RS485_INTERFACE, CONFIG_BAUD_RATE_UART0, HARDWARE_TX0_GPIO, HARDWARE_RX0_GPIO );


	rs458_vCleanBuffer( CONFIG_RS485_INTERFACE );
	rs458_vRxEnableTxDisable();

	const char * pcReceiverBuffer = rs485_pcGetBuffer( CONFIG_RS485_INTERFACE );

	queue_init( &sendToCore1Queue,	sizeof( Motor ), 5 );
	multicore_launch_core1( core1_entry );

	gpio_put( HARDWARE_LED_GPIO, true );


	#if( CONFIG_MOROT_A == CONFIG_ENABLE  )
	const char commandToFront[  ]	= "MAF";
	const char commandToBack[  ]	= "MAB";
	const char commandStop[  ]	= "MAS";
	#endif

	#if( CONFIG_MOROT_B == CONFIG_ENABLE  )
	const char commandToFront[  ]	= "MBF";
	const char commandToBack[  ]	= "MBB";
	const char commandStop[  ]	= "MBS";
	#endif

	
	while (true) {

		if( rs485_uGetBufferSize( CONFIG_RS485_INTERFACE ) > 0 ){
			
			gpio_put( HARDWARE_LED_GPIO, false );

			sleep_ms( 10 );

			char pcBuffer[ 100 ] = "";

			if ( textp_bFindString (pcReceiverBuffer, commandStop ) == true ){
				
				Motor motor = { 0,  _Stop };

				queue_add_blocking( &sendToCore1Queue, &motor );

			} else if ( textp_bGetLabelInfo (pcReceiverBuffer, commandToBack, 0, pcBuffer ) == true ){
				
				Motor motor = { atoff( pcBuffer ), _Back };
				
				if( motor.velocity <= 0 ){
					motor.velocity = 0;
					motor.direction = _Stop;
				}
				
				queue_add_blocking( &sendToCore1Queue, &motor );

			} else if ( textp_bGetLabelInfo (pcReceiverBuffer, commandToFront, 0, pcBuffer ) == true ){
				Motor motor = { atoff( pcBuffer ), _Front };

				if( motor.velocity <= 0 ){
					motor.velocity = 0;
					motor.direction = _Stop;
				}

				queue_add_blocking( &sendToCore1Queue, &motor );
			}


			rs458_vCleanBuffer( CONFIG_RS485_INTERFACE );

			gpio_put( HARDWARE_LED_GPIO, true );

		}
	}
}


void core1_entry( void ){
	servo motor1 = { HARDWARE_MOTOR1_GPIO, 0 }; 
	servo motor2 = { HARDWARE_MOTOR2_GPIO, 0 }; 


	#if( CONFIG_MOROT_A == CONFIG_ENABLE  )
	sleep_ms( 3000 ); 
	motor_vBind( &motor1 );
	sleep_ms( 1000 ); 
	motor_vBind( &motor2 );
	sleep_ms( 1000 );
	#endif

	#if( CONFIG_MOROT_B == CONFIG_ENABLE  )
	sleep_ms( 6000 ); 
	motor_vBind( &motor1 );
	sleep_ms( 1000 ); 
	motor_vBind( &motor2 );
	sleep_ms( 1000 );
	#endif

	Motor motor;
	Direction currentDirection = _Stop;

	pid pid_ma1 = {
		.fKp = CONFIG_KP,
		.fKi = CONFIG_KI,
		.fKd = CONFIG_KD,
	};

	pid pid_ma2 = {
		.fKp = CONFIG_KP,
		.fKi = CONFIG_KI,
		.fKd = CONFIG_KD,
	};

	while ( true ) {

		if( queue_try_remove(&sendToCore1Queue, &motor) == true ){
			pid_ma1.fSetPoint = motor.velocity;
			pid_ma2.fSetPoint = motor.velocity;

			if(  currentDirection != motor.direction ){
				
				currentDirection = motor.direction;

				if( currentDirection == _Back ){
					motor_vPreoareToBack( &motor1 );
					motor_vPreoareToBack( &motor2 );
				}
			}


		}

		switch ( currentDirection ) {
			case _Stop: {
				motor_vStop( &motor1 );
				motor_vStop( &motor2 );
			} break;

			case _Front: {
				motor_vToFront( &motor1, pid_ma1.fOutput );
				motor_vToFront( &motor2, pid_ma2.fOutput );
			} break;

			case _Back: {
				motor_vToBack( &motor1, pid_ma1.fOutput );
				motor_vToBack( &motor2, pid_ma2.fOutput );
			} break;

		}

		pid_ma1.fInput =  pid_fRun( &pid_ma1 );
		pid_ma2.fInput =  pid_fRun( &pid_ma2 );

		sleep_ms( 1 );

	}
	
}

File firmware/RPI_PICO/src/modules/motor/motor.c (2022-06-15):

/**
 * motor.c
 *
 *  @date Created at:	14/06/2022 15:40:32
 *	@author:	Pedro Igor B. S.
 *	@email:		pedro.igor.ifsp@gmail.com
 * 	GitHub:		https://github.com/pedro-ibs
 * 	tabSize:	8
 *
 * #######################################################################
 *   Copyright (C) Pedro Igor B. S 2021
 * -------------------------------------------------------------------
 *
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
 * Cada par de motor utiliza uma PONTE H, sendo controlado por 4 pinos de
 * saída:
 * 
 * 			      ___________
 * 			     |		|
 * 			M1 --| PONTE 1	|-- M2
 * 			     |		|
 *			M3 --| PONTE 2	|-- M4
 *			     |__________|	
 */




/* Includes ----------------------------------------------------------------------------------------------------------------------------------------------*/
#include "motor.h"

#include <zephyr.h>
#include <device.h>
#include <devicetree.h>

#include <drivers/gpio.h>



/* Setings -----------------------------------------------------------------------------------------------------------------------------------------------*/
#define M1A_NODE	DT_ALIAS( m1a )
#define M1B_NODE	DT_ALIAS( m1b )

#define M2A_NODE	DT_ALIAS( m2a )
#define M2B_NODE	DT_ALIAS( m2b )

#define M3A_NODE	DT_ALIAS( m3a )
#define M3B_NODE	DT_ALIAS( m3b )

#define M4A_NODE	DT_ALIAS( m4a )
#define M4B_NODE	DT_ALIAS( m4b )
/* Function prototype ------------------------------------------------------------------------------------------------------------------------------------*/
/* Setup -------------------------------------------------------------------------------------------------------------------------------------------------*/

static const struct gpio_dt_spec scxMotors[QTY_MOTORS] = {
	GPIO_DT_SPEC_GET(M1A_NODE, gpios),
	GPIO_DT_SPEC_GET(M1B_NODE, gpios),
	GPIO_DT_SPEC_GET(M2A_NODE, gpios),
	GPIO_DT_SPEC_GET(M2B_NODE, gpios),
	GPIO_DT_SPEC_GET(M3A_NODE, gpios),
	GPIO_DT_SPEC_GET(M3B_NODE, gpios),
	GPIO_DT_SPEC_GET(M4A_NODE, gpios),
	GPIO_DT_SPEC_GET(M4B_NODE, gpios)
};

/* -------------------------------------------------------------------------------------------------------------------------------------------------------*/

uint8_t motor_uSetup(void){

	for(uint8_t i = M1A; i<QTY_MOTORS; i++ ){
		if (!device_is_ready(scxMotors[i].port)) return 1;
		
		gpio_pin_configure_dt(&scxMotors[i], GPIO_OUTPUT_LOW);
		gpio_pin_set_dt(&scxMotors[i], false);
	}

	return 0;
}



void motor_vToFront( motors_gpio mxa, motors_gpio mxb  ){
	gpio_pin_set_dt(&scxMotors[mxa], true);
	gpio_pin_set_dt(&scxMotors[mxb], false);
}

void motor_vToBack( motors_gpio mxa, motors_gpio mxb ){
	gpio_pin_set_dt(&scxMotors[mxa], false);
	gpio_pin_set_dt(&scxMotors[mxb], true);
}

void motor_vToStop( motors_gpio mxa, motors_gpio mxb ){
	gpio_pin_set_dt(&scxMotors[mxa], true);
	gpio_pin_set_dt(&scxMotors[mxb], true);
}

void motor_vTurnoff( motors_gpio mxa, motors_gpio mxb ){
	gpio_pin_set_dt(&scxMotors[mxa], false);
	gpio_pin_set_dt(&scxMotors[mxb], false);
}

/*########################################################################################################################################################*/
/*########################################################################################################################################################*/
/*########################################################################################################################################################*/
/*-------------------------------------------------------------------- Local Functions -------------------------------------------------------------------*/
/*########################################################################################################################################################*/

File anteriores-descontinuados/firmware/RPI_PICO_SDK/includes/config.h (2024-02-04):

/**
 * config.h
 *
 *  @date Created at:	07/08/2022 14:00:24
 *	@author:	Pedro Igor B. S.
 *	@email:		pedro.igor.ifsp@gmail.com
 * 	GitHub:		https://github.com/pedro-ibs
 * 	tabSize:	8
 *
 * #######################################################################
 *   Copyright (C) Pedro Igor B. S 2021
 * -------------------------------------------------------------------
 *
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
 * Configurações gerais da aplicação
 * 
 */

/* Includes ---------------------------------------------------------------------------------------------------------------------------------------------*/
#include <stdio.h>
#include <stddef.h>
#include <ctype.h>
#include <stdlib.h>
#include "pico/stdlib.h"
#include "hardware.h"


#ifndef config_H_
#define config_H_

/* settings ----------------------------------------------------------------------------------------------------------------------------------------------*/
/* Definition --------------------------------------------------------------------------------------------------------------------------------------------*/


/* ************************************************************************************************************ */
/* CONFIGURAÇÕES DA INTERFACE SERIAL PRINCIPAL e SECUNDARIA							*/
/* ************************************************************************************************************ */
#define CONFIG_BAUD_RATE_UART0		( 115200		)
#define CONFIG_BAUD_RATE_UART1		( 19600			)
#define CONFIG_DATA_BITS		( 8			)
#define CONFIG_STOP_BITS		( 1			)
#define CONFIG_PARITY			( UART_PARITY_NONE	)
#define CONFIG_BUFFER_SIZE		( 1024			)


/* ************************************************************************************************************ */
/* CONFIGURAÇÕES DA TELEMETRIA DA FONTE DE ALIMENTAÇÃO.								*/
/* ************************************************************************************************************ */




/* ************************************************************************************************************ */
/* CONFIGURAÇÕES DO DRIVERS MOTORES										*/
/* ************************************************************************************************************ */
#define CONFIG_PWM_SYS_FREQUENCY_HZ	( 125000000		)
#define CONFIG_PWM_FREQUENCY_HZ		( 400			)
#define CONFIG_PWM_DUTY_CYCLE_START	( 0			)
#define CONFIG_KP			( 0.0751		)
#define CONFIG_KI			( 0.0009		)
#define CONFIG_KD			( 0.0003		)
#define CONFIG_PID_FRAME_HATE_MS	( 1			)
#define CONFIG_DETECT_TO_FRONT		< 0
#define CONFIG_DETECT_TO_BACK		> 0
/* ************************************************************************************************************ */
/* FORMATO DE COMUNICAÇÃO JSON (PARA FACILITAR NO NODE-RED)							*/
/* ************************************************************************************************************ */
#define CONFIG_JSON "{\"ml1\":{\"s\":%d, \"m\":%d,\"v\":%f},\"ml2\":{\"s\":%d,\"m\":%d,\"v\":%f},\"mr1\":{\"s\":%d,\"m\":%d,\"v\":%f},\"mr2\":{\"s\":%d,\"m\":%d,\"v\":%f},\"p\":{\"a\":%f,\"b\":%f,\"s\":%f}}"


/* ************************************************************************************************************ */
/* Configurações gerais da aplicação										*/
/* ************************************************************************************************************ */
#define CONFIG_QUEUE_ELEMENTS 		( 1			)
#define CONFIG_DELAY_LOOP_MS		( 1000			)
#define CONFIG_MOVING_AVERAGE		( 24			)
#define CONFIG_POWER_SUPPLY_OFFSET	( 12.00-11.7		)
#define CONFIG_POWER_SYSTEM_OFFSET	( 5.00 - 4.9		)

#endif /* config_H_ */

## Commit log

2022-05-27 projeto mecânico inicial
    [axis-M4toM8.FCStd, axis-M4toM8.stl, axis-cap.FCStd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]
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2022-05-27 correção do encaixa para do motor 'v-slot-2020-mancal-motor' rebaixo de .12mm ( resolução da Ender 3 )
    [v-slot-2020-mancal-motor.stl]
2022-05-28 coleta de medidas
    [v-slot-2020-mancal-motor-trem.FCStd]
2022-05-29 nomas medicasa e novos v-slot-2020-trem
    [v-slot-2020-fuso-M8.FCStd, v-slot-2020-tem-45mm.FCStd, v-slot-2020-tem-45mm.stl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]
2022-05-29 correção v-slot-2020-trem-6mm
    [v-slot-2020-tem-6mm.FCStd, v-slot-2020-tem-6mm.stl]
2022-05-29 correção medidas ponte-h
    [v-slot-2020-suporte-ponteH.FCStd]
2022-05-29 criado v-slot-2020-suporte-ponteH
    [v-slot-2020-suporte-ponteH.FCStd, v-slot-2020-suporte-ponteH.stl]
2022-05-29 terminado v-slot-2020-suporte-CJVL53L0XV2
    [v-slot-2020-suporte-CJVL53L0XV2.FCStd, v-slot-2020-suporte-CJVL53L0XV2.stl]
2022-05-29 terminado v-slot-2020-suporte-fuso-M8
    [v-slot-2020-fuso-M8.FCStd, v-slot-2020-suporte-fuso-M8.FCStd, v-slot-2020-suporte-fuso-M8.stl]
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2022-06-01 criado suporte para base
    [suporte-mesa-base.FCStd, suporte-mesa-base.stl]
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2022-06-01 criado case para camera
    [case-camera-frente.stl, case-camera-full.FCStd, case-camera-tras.stl]
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2022-06-02 espaco para dissipador case-camera-tras
    [case-camera-tras.FCStd, case-camera-tras.stl, suporte-alca.FCStd]
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2022-06-13 criado suporte-torre-instrumentos, iniciando configurações da rasp
    [suporte-torre-instrumentos.FCStd, suporte-torre-instrumentos.stl]
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2022-06-21 circuiro rev 1.0 correção
    [trekking-Cobre traseira.gbr, trekking-Cortes contorno.gbr, trekking-Máscara frontal.gbr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]
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2022-06-23 mesa-base modificado para novo formato do robo
    [mesa-base.FCStd, mesa-base.stl]
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2022-06-27 mesa-base corrigido
    [mesa-base.FCStd, mesa-base.stl, mesa-base170x137mm-Body.stl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]
2022-06-27 ATT placa fontes e pinos de contole
    [trekking-Cobre traseira.gbr, trekking-Cortes contorno.gbr, trekking-Máscara frontal.gbr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]
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2022-12-05 fwe d_motor_SDK tst pwm
    [trekking.kicad_sch]
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2022-12-07 driver motor rev 2
    [trekking-Cobre traseira.gbr, trekking-Cortes contorno.gbr, trekking-Máscara frontal.gbr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]
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2023-02-11 migrando de raspberry para jetson nano
    [cap-camera.FCStd, cap-camera.stl, v-slot-2020-trem-20mm.FCStd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]
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2023-03-31 atualização geral: lds, suspensão, caixa...
    [6150-3200-35000.FCStd, 6D150-3F2-35L.FCStd, 6D150-3F2-35L.stl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]
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2023-05-02 peças e alteraçõs para o motor novo
    [M4toM8-Body.stl, M4toM8.FCStd, apoio-bracket-2375-Body.stl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]
2023-05-10 peças tampa e motores
    [fixador-guia-Body.stl, fixador-guia.FCStd, suporte-M8-inferior.FCStd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]
2023-07-18 palcas identificadoras, encoder, lidar, e configurações do sistema
    [NCC-74656.stl, Voyager.stl, bocal-fixadora-Body.stl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]
2023-07-20 codigo display oled mostrador multimetro
    [NCC-74656.stl, Voyager.stl, placa-NCC-74656.FCStd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]
2023-07-21 correção medidor/mostrador, add media movel e offset
    [suporte-display-led.FCStd, suporte-display-led.stl, trekking.kicad_sch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]
2023-07-26 contole de estado de D2 a D9 do BLE SENSE 33 habilitado
    [cap-roda.FCStd, cap-roda.stl]
2023-08-05 melhorias suspencao - quadro de suspencao
    [base-M8-bracket.FCStd, haste-articulada.FCStd, haste-articulada.stl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]
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2023-11-04 Plataforma Eletrônica Para Controle Distribuído Em Rede
    [PECDR-B_Cu.gbr, PECDR-B_Mask.gbr, PECDR-B_Paste.gbr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]
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2024-02-03 anotando correções em PECDR-W e criando programa de testes
    [PECDR.kicad_pcb, PECDR.kicad_sch]
2024-02-04 arrumando arquivos e documentação
    [M4toM8-Body.stl, M4toM8.FCStd, adaptador-eixo-amortecedor-Body.stl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]
2024-02-04 dog dos esquemas de alimentação e conexões gerais
    [esquema-geral.kicad_pcb, esquema-geral.kicad_sch]
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2024-02-08 PECDR correção rs485 e de layout
    [PECDR.kicad_pcb, PECDR.kicad_sch, esquema-geral.kicad_sch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]
2024-02-13 partes variadas da rv3
    [base-fixa-20-P2.FCStd, base-fixa-20-P2.stl, espacador-22-16.FCStd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]
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2024-06-27 correção de layout e conexões no circuito PECDR-W
    [PECDR-B_Cu.gbr, PECDR-B_Mask.gbr, PECDR-B_Paste.gbr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]
2024-06-27 peças da versão 3 do robo
    [6D2-3F2-15L6.FCStd, 6D2-3F2-15L6.stl, arruela-espacadora-base.FCStd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]
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2024-06-27 atualização do esquema geral
    [esquema-geral.kicad_sch]
2024-07-05 FW para PECDR motor/subsistemas, flow do nod-RED para comtrole, suporte para adapitador RS458
    [suporte-RS485.FCStd, suporte-RS485.stl]
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2024-09-03 att rev 3 para 3.5
    [base-haste-articulada.FCStd, base-haste-articulada.stl, base-inferio-165mm.FCStd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]
2026-04-20 cor base-inferio-165mm para roxo
    [base-inferio-165mm.FCStd]
2026-04-20 criando encaixe de bateria v2
    [carco-de-encaixe-V2.FCStd, carco-de-encaixe-v1.FCStd]
2026-04-20 munando cor para roxo
    [carco-de-encaixe-V2.FCStd, carco-de-encaixe-v1.stl, limitador-lateral.FCStd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]
2026-04-20 add suporte de lampada X1 v2
    [lamp-base-X1-V1.FCStd, lamp-base-X1-V1.stl, lamp-base-X1-V2.FCStd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]
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2026-04-20 nova fixação dos motores
    [afastador-central.FCStd, afastador-central.stl, afastador-lateral.FCStd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]
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2026-04-20 mudando cor da 'bandeira'
    [placa-Voyager.FCStd]
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2026-04-20 arrumando suportes, e cores
    [placa-Voyager.FCStd, suporte-fonte-dcdc.FCStd, suporte-fusivel-reserva.FCStd]

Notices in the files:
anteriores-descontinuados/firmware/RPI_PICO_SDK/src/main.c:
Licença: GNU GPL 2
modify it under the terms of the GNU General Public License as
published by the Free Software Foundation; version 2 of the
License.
